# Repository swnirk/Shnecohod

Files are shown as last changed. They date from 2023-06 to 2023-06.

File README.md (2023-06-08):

# Shnecohod




Робот на пультеуправления, работающий по принципу шнекохода:

https://github.com/swnirk/Shnecohod/assets/54669541/ef3eb7e0-7d48-4e3a-86e5-9fca51ec2f2a

#### Задача:
- Из имеющихся компонентов построить робота для преодоления полосы препятствий
- Робот не должен приводиться в движение колесами или гусеницами

#### Компоненты:
- x2 аккумулятора 18650
- x2 модуль NRF24L01(+)
- x1 Motor Shield
- x2 Arduino Uno/Leonardo
- x1 холдер для батареек
- x2 dc-мотора с редуктором
- x1 тумблера
- x2 джойстика
- x1 потенциометр
- x1 RGB LED матрица

#### Описание решения:
Робота приводят в движения два винта архимеда, вращающихся во встречном направлении. Такая конструкция обеспечивает беспрецедентную проходимость в вязкой почве, снеге или песке.

- Основа робота вырезается из фанеры толщиной 6 мм углекислотным лазером. На неё крепятся все остальные детали
- Неподвижные детали печатаются на 3D-принтере из PLA
- Шнекороторы печатаются на 3D-принтере из TPU и крепятся на подшипники
- Питание обеспечивает блок из двух аккумуляторов 18650
- В качестве основного микроконтроллера используется Arduino Uno
- Управление осуществляется по радиоканалу. Пульт управленния также используется Arduino, а также 2 джойстика.

#### Тестирование
В ходе тестирования выявлена следующая конструктивная особенность предоставленных двигателей. При движении вперед по гладкой поверхности встречное вращение шнекороторов создает большое напряжение в области пластикового крепления двигателя. Данное крепление быстро выходит из строя. После выхода из строя движение вперед становится невозможно: вал двигателя прокручивается внутри крепления. Необходимо использовать другую конструкцию двигателей.

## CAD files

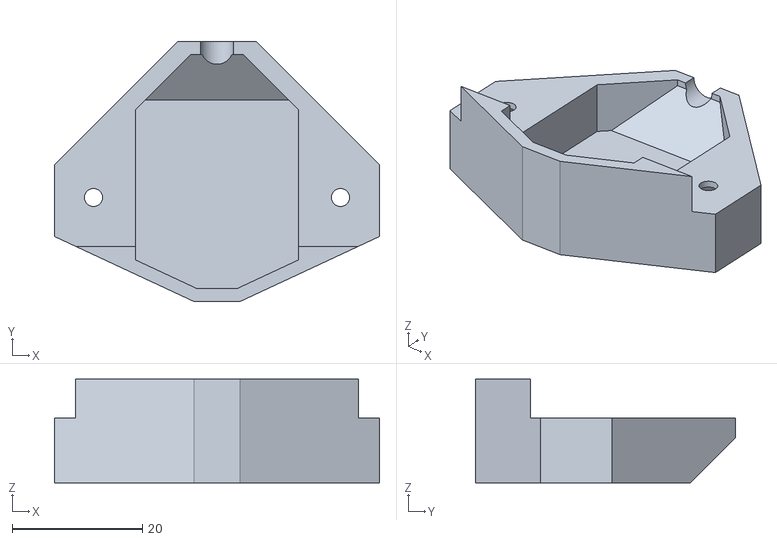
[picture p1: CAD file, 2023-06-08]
models/motor_cup.stl
50.0 x 40.0 x 16.0

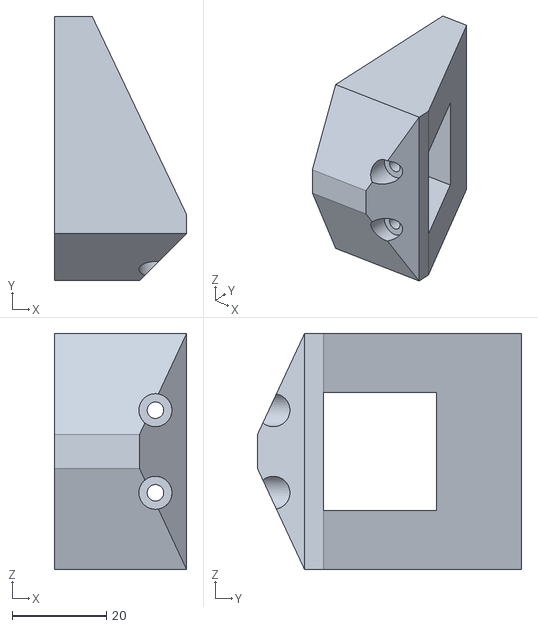
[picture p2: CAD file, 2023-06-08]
models/motor_holder.stl
28.0 x 56.0 x 50.0

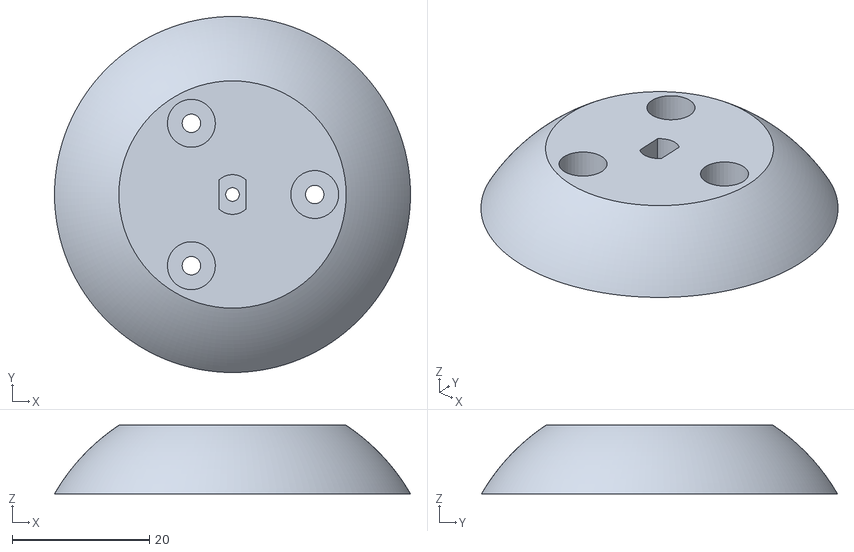
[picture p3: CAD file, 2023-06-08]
models/screw_propeller_motor_cup.stl
52.0 x 52.0 x 10.00

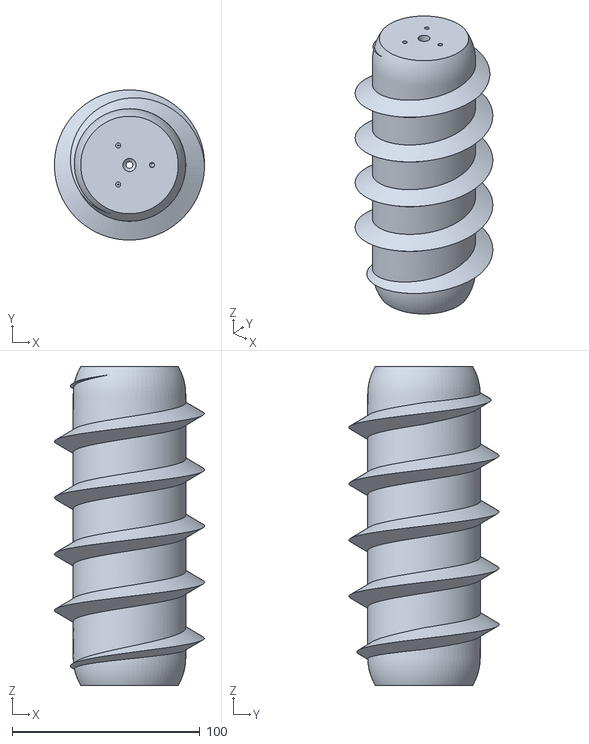
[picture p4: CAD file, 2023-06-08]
models/screw_propeller_r.stl
80.0 x 80.0 x 170.0

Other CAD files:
models/screw_propeller_l.stl

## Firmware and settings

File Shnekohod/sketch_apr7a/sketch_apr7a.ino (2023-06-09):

#include <SPI.h>
#include <nRF24L01.h>
#include <RF24.h>

RF24 radio(9, 10);
int data[5];  

const int xPin = A1;
const int yPin = A0;
const int buttonPin = 4;
const int ptmrPin = A2;
const int tumblrPin = 0;

int xPosition = 0;
int yPosition = 0;
int buttonState = 0;
int tumblrState = 0;
int ptmrState = 0;

int speed = 0;
int direction = 0;
                                
void setup(){
    radio.begin();
    radio.setChannel(5);                                  // Указываем канал передачи данных (от 0 до 127), 5 - значит передача данных осуществляется на частоте 2,405 ГГц (на одном канале может быть только 1 приёмник и до 6 передатчиков)
    radio.setDataRate     (RF24_1MBPS);                   // Указываем скорость передачи данных (RF24_250KBPS, RF24_1MBPS, RF24_2MBPS), RF24_1MBPS - 1Мбит/сек
    radio.setPALevel      (RF24_PA_HIGH);                 // Указываем мощность передатчика (RF24_PA_MIN=-18dBm, RF24_PA_LOW=-12dBm, RF24_PA_HIGH=-6dBm, RF24_PA_MAX=0dBm)
    radio.openWritingPipe (0x3234567890LL);               // Открываем трубу с идентификатором 0x1234567890 для передачи данных (на одном канале может быть открыто до 6 разных труб, которые должны отличаться только последним байтом идентификатора)
    
    pinMode(xPin, INPUT);
    pinMode(yPin, INPUT);
    pinMode(buttonPin, INPUT_PULLUP);
    pinMode(tumblrPin, INPUT);
    pinMode(ptmrPin, INPUT);
    Serial.begin(9600);

}
void loop(){
    xPosition = analogRead(xPin) / 4;
    yPosition = analogRead(yPin) / 4;
    buttonState = 34;//digitalRead(buttonPin);
    tumblrState = 35;//digitalRead(tumblrPin);
    ptmrState = 36;//analogRead(ptmrPin); 
    tumblrState = digitalRead(2);
    


    data[0] = yPosition;
    data[1] = xPosition;
    data[2] = speed;
    data[3] = !buttonState;
    data[4] = tumblrState;
    data[5] = ptmrState;
    radio.write(&data, sizeof(data));                    // указывая сколько байт массива мы хотим отправить. с проверкой их доставки: if( radio.write(&data, sizeof(data)) ){ приняты;}else{не приняты приёмником;}
    //Serial.println(ptmrState);
    //Serial.println(speed);
    delay(100);
}

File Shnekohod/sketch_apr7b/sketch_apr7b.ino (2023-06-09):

#include <SPI.h>                                         
#include <nRF24L01.h>                                    
#include <RF24.h>  
#include <Adafruit_NeoPixel.h>
#ifdef __AVR__
  #include <avr/power.h>
#endif
#define PIN        3
#define NUMPIXELS 64

Adafruit_NeoPixel pixels(NUMPIXELS, PIN, NEO_GRB + NEO_KHZ800);
#define DELAYVAL 500   

#include "Common.h"
#include "MotorControl.h"

RF24 radio(8, 9); // nRF24L01+ (CE, CSN)
int data[5]; 

void setup(){
  initMotorControl();
  Serial.begin(9600);
    
  radio.begin();                                        
  radio.setChannel(5);                                  // Указываем канал приёма данных (от 0 до 127), 5 - значит приём данных осуществляется на частоте 2,405 ГГц (на одном канале может быть только 1 приёмник и до 6 передатчиков)
  radio.setDataRate     (RF24_1MBPS);                   // Указываем скорость передачи данных (RF24_250KBPS, RF24_1MBPS, RF24_2MBPS), RF24_1MBPS - 1Мбит/сек
  radio.setPALevel      (RF24_PA_HIGH);                 // Указываем мощность передатчика (RF24_PA_MIN=-18dBm, RF24_PA_LOW=-12dBm, RF24_PA_HIGH=-6dBm, RF24_PA_MAX=0dBm)
  radio.openReadingPipe (1, 0x3234567890LL);            // Открываем 1 трубу с идентификатором 0x1234567890 для приема данных (на одном канале может быть открыто до 6 разных труб, которые должны отличаться только последним байтом идентификатора)
  radio.startListening  ();                             // Включаем приемник, начинаем прослушивать открытую трубу
  //  radio.stopListening   ();                         // Выключаем приёмник, если потребуется передать данные

#if defined(__AVR_ATtiny85__) && (F_CPU == 16000000)
  clock_prescale_set(clock_div_1);
#endif

  pixels.begin();
}

void loop(){
  Command cmd;
  uc tmp[2] = {37, 49};
  uc test = 0;
    if(radio.available()){                                // Если в буфере имеются принятые данные
        radio.read(&data, sizeof(data));                  // Читаем данные в массив data и указываем сколько байт читать
        setPowerOnMotors(data[0], data[1]);
        Serial.println(data[4]);
        Serial.println(data[0]);
        Serial.println(data[1]);         
    }
  pixels.clear();
  if(data[4]) {
    for(int i=0; i<NUMPIXELS; i++) {
    pixels.setPixelColor(i, pixels.Color(16, 16, 16));
    }
    pixels.show();
  } else {
    for(int i=0; i<NUMPIXELS; i++) {
    pixels.setPixelColor(i, pixels.Color(0, 0, 0));
    }
    pixels.show();

  }
}

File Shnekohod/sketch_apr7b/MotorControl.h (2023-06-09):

const int M_LEFT_PIN = 6;
const int M_RIGHT_PIN = 5;
const int ROT_RIGHT_PIN = 4;
const int ROT_LEFT_PIN = 7;
const int JOY_PIN = A0;


enum MOTOR {LEFT, RIGHT};
enum ROTATION {FORWARD, BACKWARD};

void setRotation(int rotationPin, ROTATION rotation);
void setSpeedRotation(MOTOR motor, ROTATION rotation, int speed);

void initMotorControl() {
  pinMode(M_LEFT_PIN, OUTPUT);
  pinMode(M_RIGHT_PIN, OUTPUT);
  pinMode(ROT_RIGHT_PIN, OUTPUT);
  pinMode(ROT_LEFT_PIN, OUTPUT);
}

int16_t rattlingOff(int16_t value)
{
  if (abs(value) < 5) 
    return 0;
  return value;  
}

int16_t rattlingOffCenter(int16_t value)
{
  if (value > 140)
    return (value - 128) * 2 + 1;
  if (value < 110)
    return (127 - value) * 2 + 1;
  return 0;  
}

void setPowerOnMotors(int16_t leftMotor, int16_t rightMotor)
{
  int16_t middle = 256 / 2;

  setSpeedRotation(LEFT, (leftMotor - middle) > 0 ? FORWARD : BACKWARD , rattlingOffCenter(leftMotor));
  setSpeedRotation(RIGHT, (rightMotor - middle) > 0 ? FORWARD : BACKWARD, rattlingOffCenter(rightMotor));
}

void setRotation(int rotationPin, ROTATION rotation)
{
  if (rotation)
    digitalWrite(rotationPin, HIGH);
  else
    digitalWrite(rotationPin, LOW);
}

void setSpeedRotation(MOTOR motor, ROTATION rotation, int speed)
{
  int rotationPin = -1;
  int motorPin = -1;

  if (motor == LEFT)
  {
    rotationPin = ROT_LEFT_PIN;
    motorPin = M_LEFT_PIN;
  }
  else
  {
    rotationPin = ROT_RIGHT_PIN;
    motorPin = M_RIGHT_PIN;
  }
  setRotation(rotationPin, rotation);
  analogWrite(motorPin, speed);
}
